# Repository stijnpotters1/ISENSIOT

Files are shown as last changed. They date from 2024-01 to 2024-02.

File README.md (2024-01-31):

# ISENSIOT-robot-arm

This is an arduino directory for the hand gesture controlled robot arm

## Bluetooth configuratie:
### Circuits
Gebruik tijdens de **configuratie** voor de arduino **uno** tijdelijk dit circuit. 
Schermafbeelding 2023-12-11 174135

Gebruik tijdens de **configuratie** voor de arduino **nano** tijdelijk dit circuit. 
Schermafbeelding 2023-12-11 172838

 ### Slave (uno):

 1. Houdt het knopje van de bluetooth module in, waar je de slave van wilt maken (in ons geval de uno).
 2. Zet power aan en check of het lampje van de hc-05 module per 2 seconde 1 keer knippert
 3. **upload** het **HC05-CONFIGURATION** schema
 5. Open de serial monitor, en zorg dat rechts onderin de baud rate op 38400 staat, en links daarvan staat op "both NL and CR"
 5. Test nu of de configuratie werkt, door "**AT**" in de serial monitor in te voeren. Als het goed is krijg je "**OK**" terug.
 6. Check of je op een 38400 baud rate zit met de command: "**AT+UART?**", zo niet, gebruik command: "**AT+UART=38400,0,0**".
 7. Check nu of je hc-05 module in slave mode staat met "**AT+ROLE?**", als het goed is wordt er "**+ROLE:0**" gereturnt. (dat komt doordat dit de 
    default configuration is.)
 8. Vraag nu het mac adres van je HC05 module op met "**AT+ADDR?**". Schrijf op, of bewaar het mac adres wat je terug krijgt.
 9. Verander nu je circuit naar deze opstelling. (dit is het vaste circuit wat we gebruiken voor de robot arm):
     Schermafbeelding 2023-12-11 174157

 ### Master (Nano).

 10. Houdt het knopje van de bluetooth module in, waar je de master van wilt maken (in ons geval de nano).
 11. Zet power aan en check of het lampje van de hc-05 module per 2 seconde 1 keer knippert
 12. **upload** het **HC05-CONFIGURATION** schema 
 13. Open de serial monitor, en zorg dat rechts onderin de baud rate op 38400 staat, en links daarvan staat op "both NL and CR"
 14. Test nu of de configuratie werkt, door "**AT**" in de serial monitor in te voeren. Als het goed is krijg je "OK" terug.
 15. Check of je op een 38400 baud rate zit met de command: "**AT+UART?**", zo niet, gebruik command: "**AT+UART=38400,0,0**".
 16. Typ nu in de serial monitor: "**AT+ROLE=1**". hiermee verander je de default waarde (slave) naar een master.
 17. Typ nu in de serial monitor: "**AT+CMODE=0**". hiermee zet je de verbinding modus naar een adres op fixed.
 18. Nu kan je de command: "**AT+BIND=XXXX,XX,XXXXXX**" gebruiken". **LET OP**. voer ipv "XXXX,XX,XXXXXX", het mac address in wat je bij **stap 8** hebt 
     opgeschreven. Ook moet je er op letten dat je **kommas** plaatst tussen de characters ipv een "-".
 19. Nu zijn de master en slave modules geconfigureerd. (alleen aan elkaar, omdat je de master specifiek aan het mac address van de slave hebt gekoppeld. Dit 
     zorgt voor extra security. Mocht het je niets uitmaken, kan je de command: "AT+CMODE=1" gebruiken. De slave kan zich nu aan verschillende HC05 master  
     modules koppelen. maar voor nu gebruiken we dit even niet).
 20. Verander nu je circuit naar deze opstelling. (dit is het vaste circuit wat we gebruiken voor de handschoen)
     Schermafbeelding 2023-12-11 173013

 ### Algemeen:
 
 21. Als je nu de twee HC05 modules aan stroom zet. gaan ze nu in de derde stand. Dit is de gekoppelde stand. Dit kun je herkennen doordat de lampjes op beide 
     modules, nu twee keer synchrone gaan knipperen. 
 22. upload op de **Arduino Nano** de **Glove.ino** code.
 23. upload op de **Arduino Uno** de **Robotarm.uno** code.

### Voltooid!
 24. als het goed is heb je nu een werkende bluetooth connectie. (Dit kan je testen door te checken of de messages van de arduino nano in de seriele monitor van 
     de arduino uno binnen komen.

## Final version robot arm en handschoen circuit diagrammen:
### Robotarm


### Handschoen


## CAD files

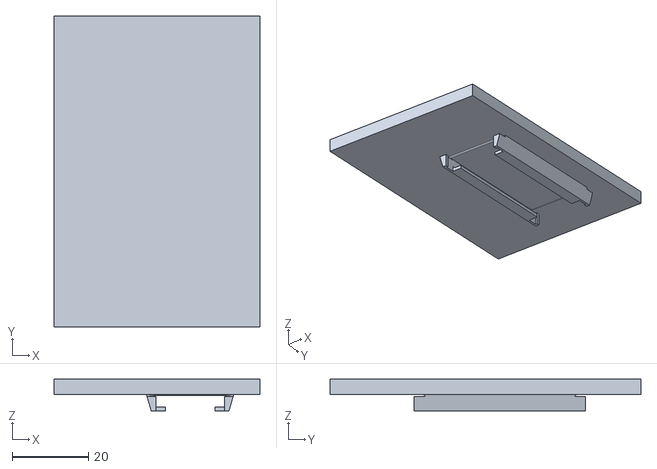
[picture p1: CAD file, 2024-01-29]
Files/BlenderFiles/Glove/FINALBreadBoardholder.stl
54.0 x 81.5 x 8.33

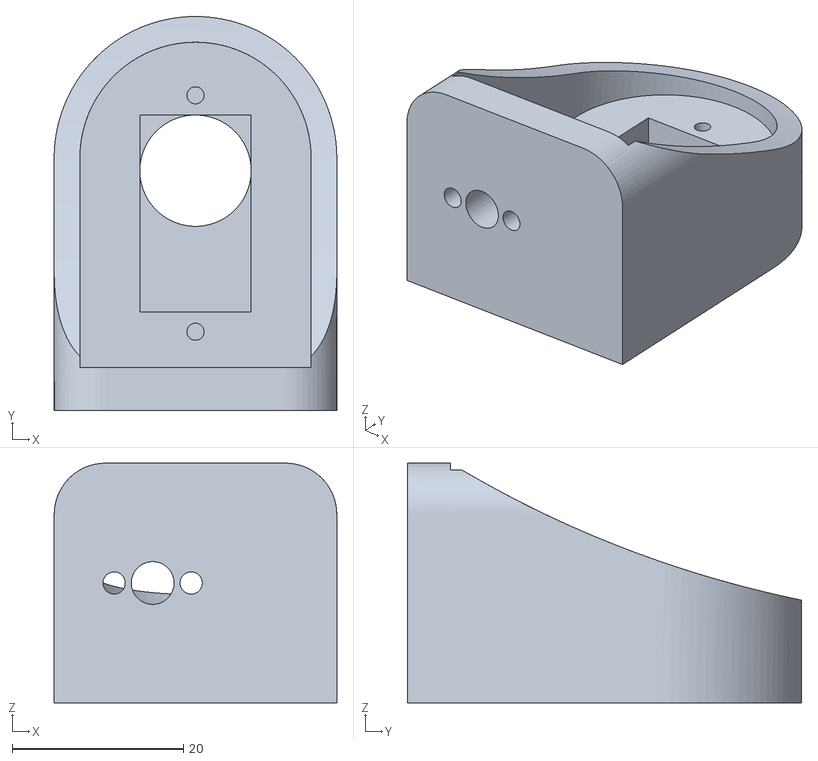
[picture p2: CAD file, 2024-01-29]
Files/BlenderFiles/Robotarm/FINALArm 03.STL
33.0 x 46.0 x 28.0

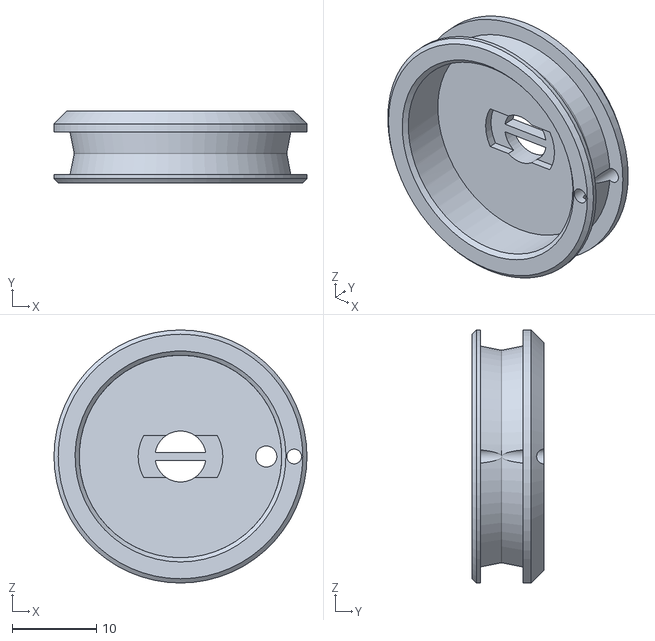
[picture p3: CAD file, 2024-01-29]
Files/BlenderFiles/Glove/FINALHapticSpool_Proto4.1.STL
30.0 x 8.50 x 30.0

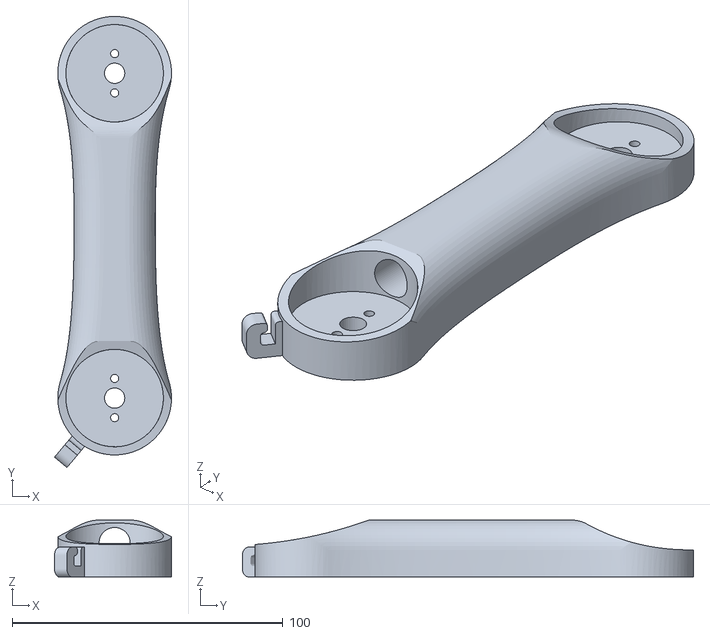
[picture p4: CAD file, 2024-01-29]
Files/BlenderFiles/Robotarm/FINALArm 01.STL
43.2 x 166.7 x 21.0

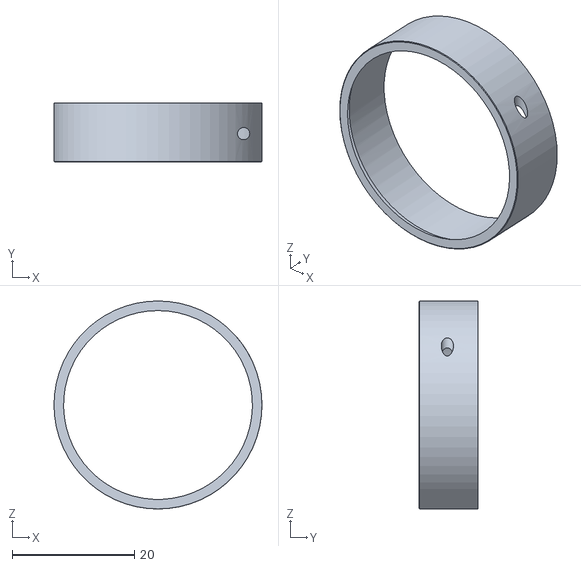
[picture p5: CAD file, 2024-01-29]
Files/BlenderFiles/Glove/FINALSpoolCover.STL
34.0 x 9.63 x 34.0

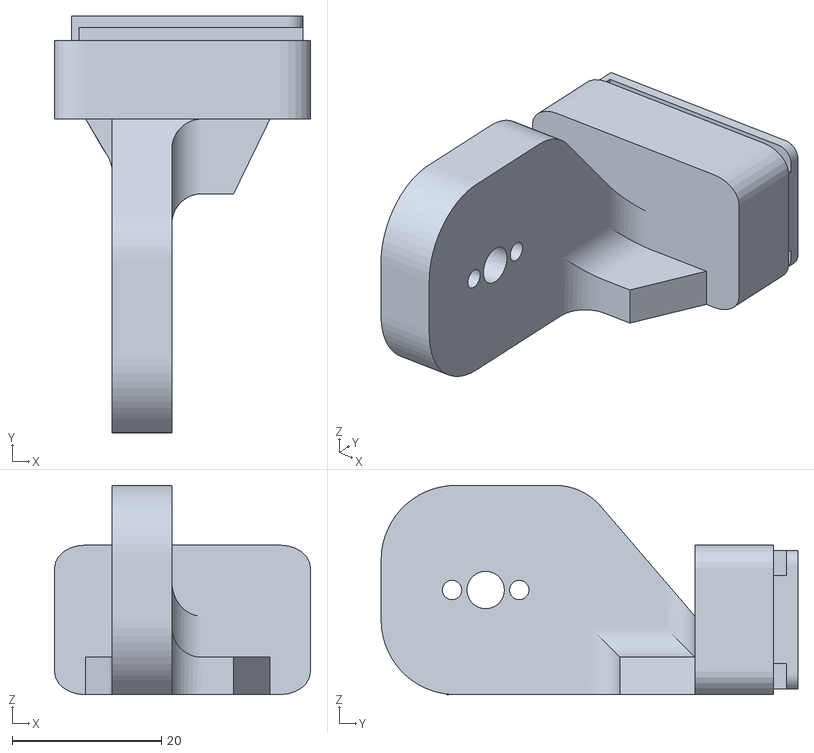
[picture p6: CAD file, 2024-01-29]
Files/BlenderFiles/Robotarm/FINALgripperbase.stl
34.3 x 55.8 x 28.0

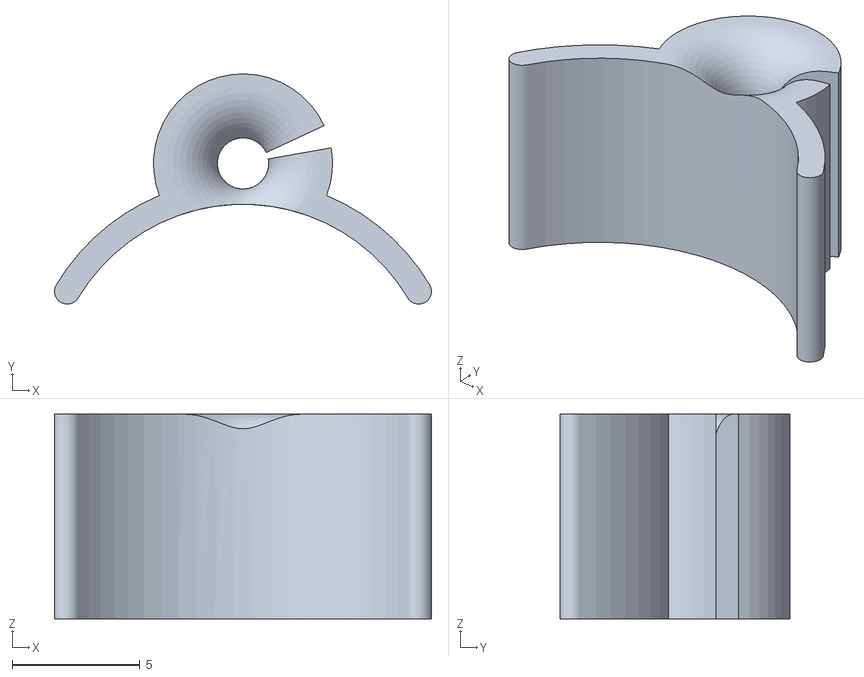
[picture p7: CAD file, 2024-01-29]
Files/BlenderFiles/Glove/FINALGuideNode.STL
14.7 x 9.00 x 8.00

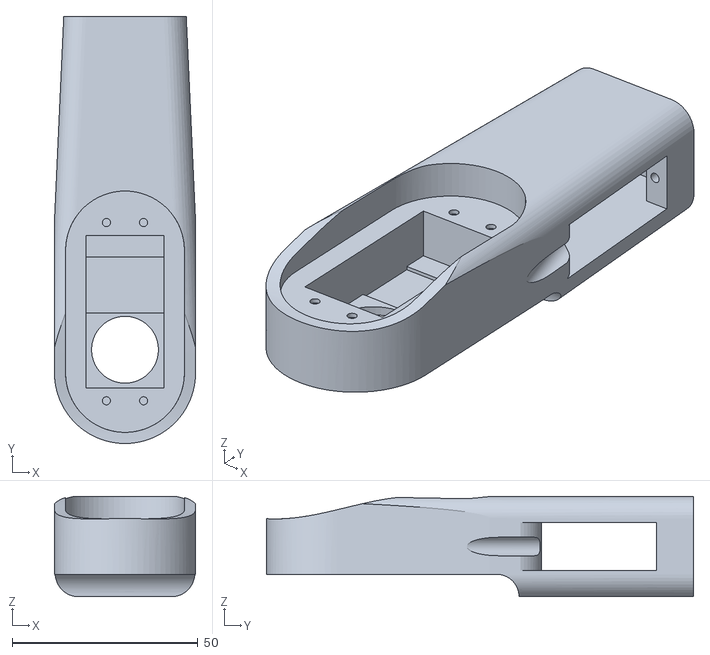
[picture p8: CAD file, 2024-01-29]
Files/BlenderFiles/Robotarm/FINALarm 02.stl
38.0 x 115.0 x 27.0

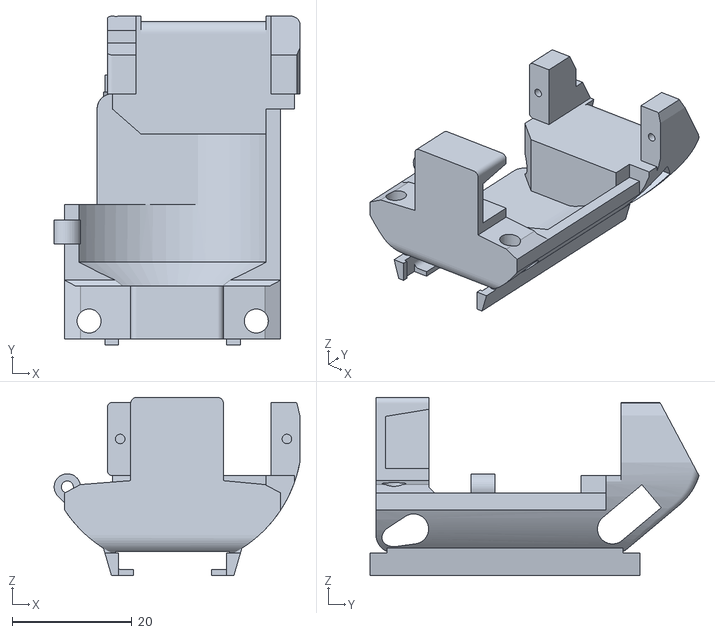
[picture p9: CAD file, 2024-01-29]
Files/BlenderFiles/Glove/FINALHapticModule.STL
41.0 x 54.9 x 29.8

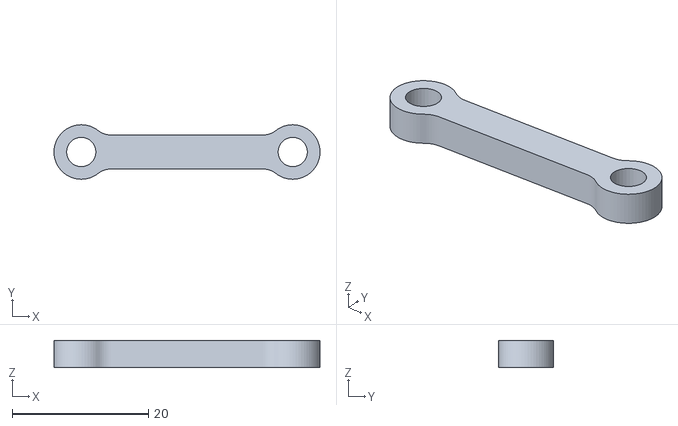
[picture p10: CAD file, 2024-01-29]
Files/BlenderFiles/Robotarm/FINALgripperlink2.15.stl
39.0 x 8.00 x 4.00

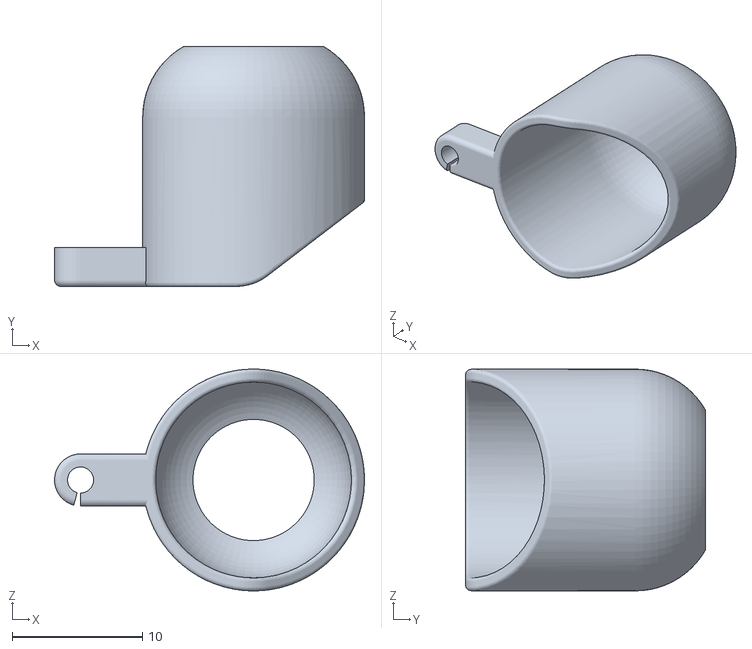
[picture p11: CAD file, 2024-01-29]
Files/BlenderFiles/Glove/FINALEndCap.STL
23.8 x 18.4 x 17.0

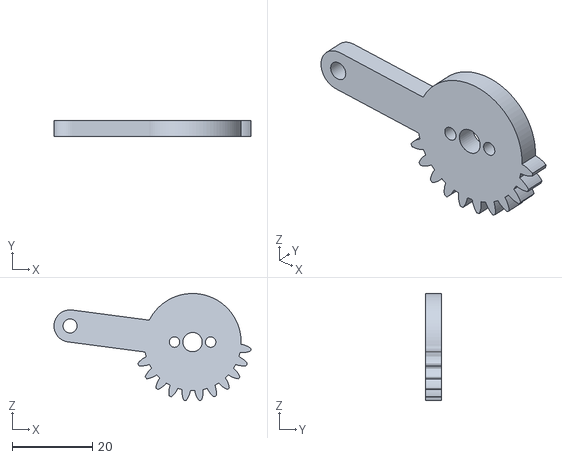
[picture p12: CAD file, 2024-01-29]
Files/BlenderFiles/Robotarm/FINALgear2.STL
49.0 x 4.00 x 26.6

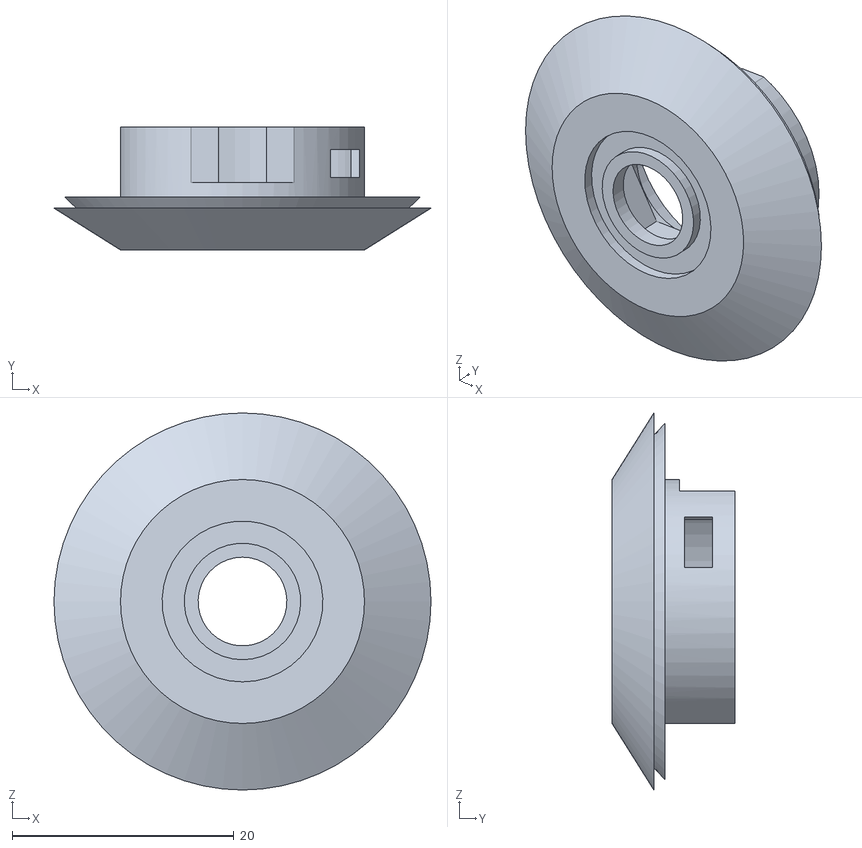
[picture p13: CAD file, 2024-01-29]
Files/BlenderFiles/Glove/FINALTensioner.STL
34.0 x 11.1 x 34.0

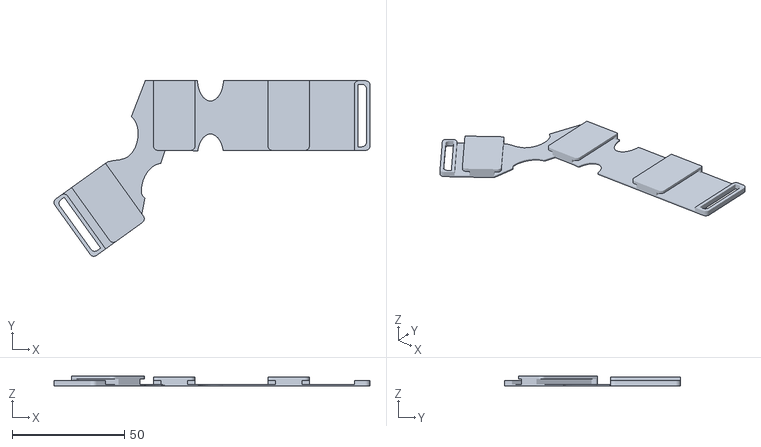
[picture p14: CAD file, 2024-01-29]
Files/BlenderFiles/Glove/FINALhandschoen.stl
140.6 x 78.1 x 4.61

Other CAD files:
Files/BlenderFiles/Robotarm/FINALgear1.stl
Files/BlenderFiles/Robotarm/FINALbase.stl
Files/BlenderFiles/Robotarm/FINALgripperattatchment.stl
Files/BlenderFiles/Robotarm/FINALwaist.stl
Files/BlenderFiles/Glove/handschoen.blend
Files/BlenderFiles/Robotarm/FINALgripper.stl
Files/BlenderFiles/Robotarm/arm2withmargin.blend
Files/BlenderFiles/Robotarm/baseholder.blend
Files/BlenderFiles/Robotarm/longerholesbase.blend
Files/BlenderFiles/Robotarm/margin to waist.blend
Files/BlenderFiles/Robotarm/sideways gripper attatchment.blend

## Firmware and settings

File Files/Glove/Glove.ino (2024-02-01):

#include <SoftwareSerial.h>
#include <MPU6050.h>
#include "I2Cdev.h"
#include <Wire.h>

#define TX 2
#define RX 3

SoftwareSerial BTSerial(TX, RX);
MPU6050 mpu;

const float OFFSET_GY_X = 46;
const float OFFSET_GY_Y = -10;
const float OFFSET_GY_Z = 46;
const float OFFSET_ACCEL_X = 990;
const float OFFSET_ACCEL_Y = -864;
const float OFFSET_ACCEL_Z = 939;

int16_t ax, ay, az, gx, gy, gz;
String servoDegreesOne, servoDegreesTwo, servoDegreesThree, servoDegreesFour, servoDegreesFive, servoDegreesSix; 

float totalRotationX = 0.0;
float totalRotationY = 0.0;
float totalRotationZ = 0.0;

unsigned long previousMillisGyro = 0;

const float GRAVITY = 9.81;  // Acceleration due to gravity in m/s^2
unsigned long previousMillisAcceleration = 0;

float totalDistanceX = 0.0;
float totalDistanceY = 0.0;
float totalDistanceZ = 0.0;
  
const int POTENTIOMETER_PIN_NUMBER_LEFT_RIGHT = A1;
const int POTENTIOMETER_PIN_NUMBER_FORWARD_BACKWARD = A2;
const int POTENTIOMETER_PIN_NUMBER_GRIPPER = A7;

struct MinMax {
  int min;
  int max;
};

struct MinMax servoPWMReachZeroToSixHunderd = {120, 600};
struct MinMax potPWMReachGripper = {300, 120};
struct MinMax servoPWMReachSixHunderdToZero = {600, 120};

struct MinMax joyStickReach = {0, 1000};

struct MinMax wristReachReciprocating = {-150, 150};
struct MinMax wristReachRotation = {-600, 600};
struct MinMax upDownReach = {-3500, 3500};
struct MinMax servoGripper = {0, 240};

unsigned long timerMillis = 0;


struct MinMax pot = {0, 200}; //Eerst kijken wat echte waardes zijn
int servoDelta = 0;
int potentiometerDelta = 0;
int previousPotentiometerMeasurement = 0;


void initializeGyro() {
  mpu.initialize();
  mpu.setDLPFMode(MPU6050_DLPF_BW_5);
  
  mpu.setXGyroOffset(OFFSET_GY_X);
  mpu.setYGyroOffset(OFFSET_GY_Y);
  mpu.setZGyroOffset(OFFSET_GY_Z);
  mpu.setXAccelOffset(OFFSET_ACCEL_X);
  mpu.setYAccelOffset(OFFSET_ACCEL_Y);
  mpu.setZAccelOffset(OFFSET_ACCEL_Z);
  delay(100);
}  

String gyroMovement(int axis, struct MinMax wristReach, struct MinMax servoPWMReach, float& totalRotation) {
   unsigned long currentMillis = millis();  
   float elapsedTime = (currentMillis - previousMillisGyro) / 1000.0;

   float rotationChange = axis * elapsedTime;
   totalRotation += (int)rotationChange;

   int mappedRotation = map(totalRotation, wristReach.min, wristReach.max, servoPWMReach.min, servoPWMReach.max);

   if (mappedRotation >= 600) {
     mappedRotation = 600;
   }
   else if (mappedRotation <= 0) {
     mappedRotation = 0;
   }

   previousMillisGyro = currentMillis;

   return (String) mappedRotation;
}

String measureGripperMovement(struct MinMax potReach, struct MinMax servoReach) {
  int currentPotentiometerMeasurement = analogRead(POTENTIOMETER_PIN_NUMBER_GRIPPER);

  currentPotentiometerMeasurement = constrain(currentPotentiometerMeasurement, potReach.min, potReach.max);

  int gripperValue = map(currentPotentiometerMeasurement, potReach.min, potReach.max, servoReach.min, servoReach.max);

  return (String)gripperValue;
}

void sendData() {
  String message = servoDegreesOne + "," + servoDegreesTwo + "," + servoDegreesThree + "," + servoDegreesFour + "," + servoDegreesFive + "," + servoDegreesSix + ";";
  Serial.println(message);
  
  int message_len = message.length() + 1; 

  char char_array[message_len];
  
  message.toCharArray(char_array, message_len);

  BTSerial.write(char_array);
}

void setup() {
  // put your setup code here, to run once:
  Serial.begin(38400);
  BTSerial.begin(115200);
  initializeGyro();
  timerMillis = millis();
}


String potmeterMovement(int PotPinNumber, struct MinMax potReach, struct MinMax servoReach) {
  int potmeterValue = analogRead(PotPinNumber);
  int servoValue = map(potmeterValue, potReach.min, potReach.max, servoReach.min, servoReach.max );
  
  return (String)servoValue;
}


void loop() {
  mpu.getMotion6(&ax, &ay, &az, &gx, &gy, &gz);
  unsigned long currentMillis = millis();  
  
  servoDegreesOne = gyroMovement(gz, upDownReach,  servoPWMReachSixHunderdToZero, totalRotationZ);
  servoDegreesTwo = potmeterMovement(POTENTIOMETER_PIN_NUMBER_FORWARD_BACKWARD, joyStickReach, servoPWMReachZeroToSixHunderd);
  servoDegreesThree = potmeterMovement(POTENTIOMETER_PIN_NUMBER_LEFT_RIGHT, joyStickReach, servoPWMReachZeroToSixHunderd); 
  servoDegreesFour = gyroMovement(gy, wristReachRotation,  servoPWMReachZeroToSixHunderd, totalRotationY);
  servoDegreesFive = gyroMovement(gx, wristReachReciprocating,  servoPWMReachZeroToSixHunderd, totalRotationX);
  servoDegreesSix = measureGripperMovement(pot, potPWMReachGripper);
 
  if (currentMillis - timerMillis >= 2000)  //test whether the period has elapsed
  {
    sendData();
    timerMillis = currentMillis;  //IMPORTANT to save the start time of the current LED state.
  } 
}

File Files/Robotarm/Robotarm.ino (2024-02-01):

#include <Adafruit_PWMServoDriver.h>
#include <Wire.h>
#include <SoftwareSerial.h>

#define TX 2
#define RX 3
#define N_SERVO_MOTORS 6

Adafruit_PWMServoDriver servoDriver = Adafruit_PWMServoDriver();
SoftwareSerial BTSerial(TX, RX);

const int STEP_PRECISION_SERVO = 1;
const int MAX_STEPS_PER_MOVEMENT_TICK = 10;
const int SERVO_DELAY_PER_STEP = 1;
const int PWM_FREQUENCY = 60;

String incomingCommand = "";

struct servoMotor {
  const int SERVO_PIN_NR;
  const int MAX_PWM_VALUE;
  const int MIN_PWM_VALUE;
  int currentPWMValue;
  int nextPWMValue;
};

// Order of the servos is base, waist, arm1, arm2, arm3, gripper
struct servoMotor servos[N_SERVO_MOTORS] = {{0, 600, 120, 340, 340}, {2, 600, 120, 400, 400}, {4, 600, 120, 450, 450}, {6, 600, 120, 340, 340}, {8, 600, 120, 120, 120}, {10, 300, 120, 240, 240}};

void InitializeServoDriver() {
  Serial.begin(38400);
  servoDriver.begin();
  servoDriver.setPWMFreq(PWM_FREQUENCY);
  delay(10);
}

void InitializeBluetoothModule() {
  BTSerial.begin(115200);
}

void MoveServoToPosition(int newServoPosition, int &currentServoPosition, int servoPinNr) {
  if(newServoPosition < currentServoPosition) {
    for (int i = 0; i < MAX_STEPS_PER_MOVEMENT_TICK; i++) {
      int pos = currentServoPosition - STEP_PRECISION_SERVO;

      if(pos < newServoPosition) {
        pos = newServoPosition;
      }

      servoDriver.setPWM(servoPinNr, 0, pos);
      delay(SERVO_DELAY_PER_STEP);
      currentServoPosition = pos;
    }  
  } else if (newServoPosition > currentServoPosition) {
    for (int i = 0; i < MAX_STEPS_PER_MOVEMENT_TICK; i++) {
      int pos = currentServoPosition + STEP_PRECISION_SERVO;

      if(pos > newServoPosition) {
        pos = newServoPosition;
      }

      servoDriver.setPWM(servoPinNr, 0, pos);
      delay(SERVO_DELAY_PER_STEP);
      currentServoPosition = pos;
    }  
  }
}

void MoveServos() {
  for (int i = 0; i < N_SERVO_MOTORS; i++) {
    if(servos[i].currentPWMValue != servos[i].nextPWMValue) {
      MoveServoToPosition(servos[i].nextPWMValue, servos[i].currentPWMValue, servos[i].SERVO_PIN_NR);
    }
  }
}

void SetNextPWMValue(int index, int value) {
  if(servos[index].MIN_PWM_VALUE > value) {
    servos[index].nextPWMValue = servos[index].MIN_PWM_VALUE;
  } else if(servos[index].MAX_PWM_VALUE < value) {
    servos[index].nextPWMValue = servos[index].MAX_PWM_VALUE;
  } else {
    servos[index].nextPWMValue = value;
  }
}

void setup() {
  InitializeServoDriver();
  InitializeBluetoothModule();
}

void loop() {   
  if (BTSerial.available() > 0) {
    // read the incoming byte:
    incomingCommand = BTSerial.readString();
    int servoCounter = 0;
    // say what you got:
    Serial.print("I received: ");
    Serial.println(incomingCommand);

    incomingCommand = incomingCommand.substring(0, incomingCommand.length() - 1);

    int command = incomingCommand.indexOf(';');
    
    while (command != -1) {
        incomingCommand = incomingCommand.substring(command + 1);
        command = incomingCommand.indexOf(';');
    }

    Serial.println("done");
    Serial.println(incomingCommand);

    while (incomingCommand.length() > 0) {
      int index = incomingCommand.indexOf(',');
      if (index == -1) {
        if(servoCounter == (N_SERVO_MOTORS - 1)) {
          int value = incomingCommand.substring(0, incomingCommand.length()).toInt();
          SetNextPWMValue(servoCounter, value);
          Serial.println(incomingCommand.substring(0, incomingCommand.length()));
        } else {
          Serial.println("Incomming command format error!");
        }
        break;
      } else {
        Serial.println(incomingCommand.substring(0, index));
        int value = incomingCommand.substring(0, index).toInt();
        SetNextPWMValue(servoCounter, value);
        incomingCommand = incomingCommand.substring(index + 1);
        servoCounter++;
      }
    }
  }

  MoveServos();
}

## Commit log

2023-12-11 fix: organized coniguration code
    [HC05_configuration.ino]
2024-01-22 added gripper function
2024-01-29 added gyro initialize function
2024-01-29 feat: added function for gyroscope
2024-01-29 fix: updated senddata function
    [Glove.ino]
2024-01-29 fix: updated constant loop for new functions
    [Glove.ino]
2024-01-29 Toevoegen blender en STL files
    Alleen finale STL bestanden.
    [FINALArm 01.STL, FINALArm 03.STL, FINALBreadBoardholder.stl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]
2024-01-31 Update README.md
    added circuit diagrams
